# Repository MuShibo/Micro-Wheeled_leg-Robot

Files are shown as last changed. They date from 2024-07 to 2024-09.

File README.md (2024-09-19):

# Micro-Wheeled_leg-Robot
> **The smallest two-wheeled-leg robot!**
>
> Video：[[自制]首款桌面级双轮腿机器人](https://www.bilibili.com/video/BV1io4y1q73L/?spm_id_from=333.999.0.0)
>

| Real Robot | 3D Design |
| --- | --- |
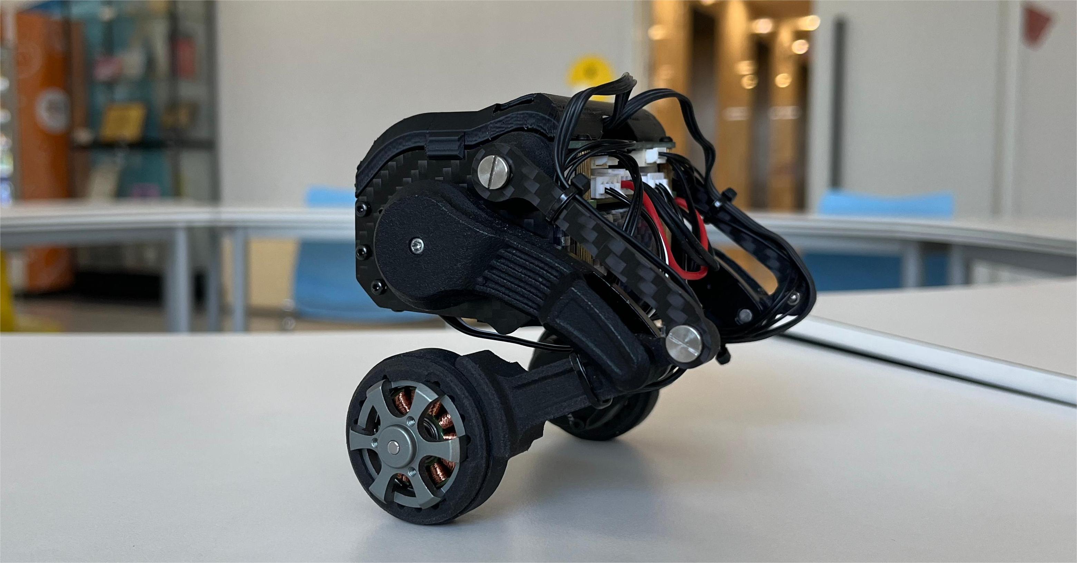
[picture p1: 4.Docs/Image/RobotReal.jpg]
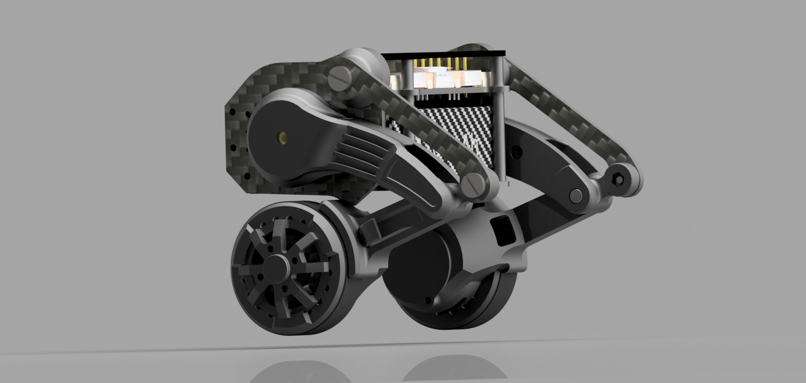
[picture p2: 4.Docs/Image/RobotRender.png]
|  |  |

[中文文档](README_CN.md)

### Mechanical Structure Documentation

* The file "OriginalRobotModel.stp" is the robot model file.
* The "Parts-Manufactured" folder contains parts that need to be processed and produced by yourself, including 3D printing, CNC, and panel cutting.
* The "Parts-Purchased" folder contains parts that need to be purchased.

### PCB Documentation

* There are four PCBs that need to be fabricated; the circuit boards provide both the schematic and PCB source files, and the IDE used is [LCEDA](https://lceda.cn/).
* The main control board is based on the ESP32, with the brushless motor driver chip being the L6234PD013TR. 
* The encoder chip used is the AS5600, communicating with the main control board via the I2C interface.
* The IMU used is the MPU6050 module, which shares the same I2C interface with the right-side encoder.
* The servo debugging board unifies the two serial lines into one signal line, completing the task through time-division multiplexing to send and receive data.
* In addition, you will need three GH1.25 4PIN double-ended cables, with a recommended length of 15cm. These need to be purchased separately.

| Wire Connection | 
| ------------ |
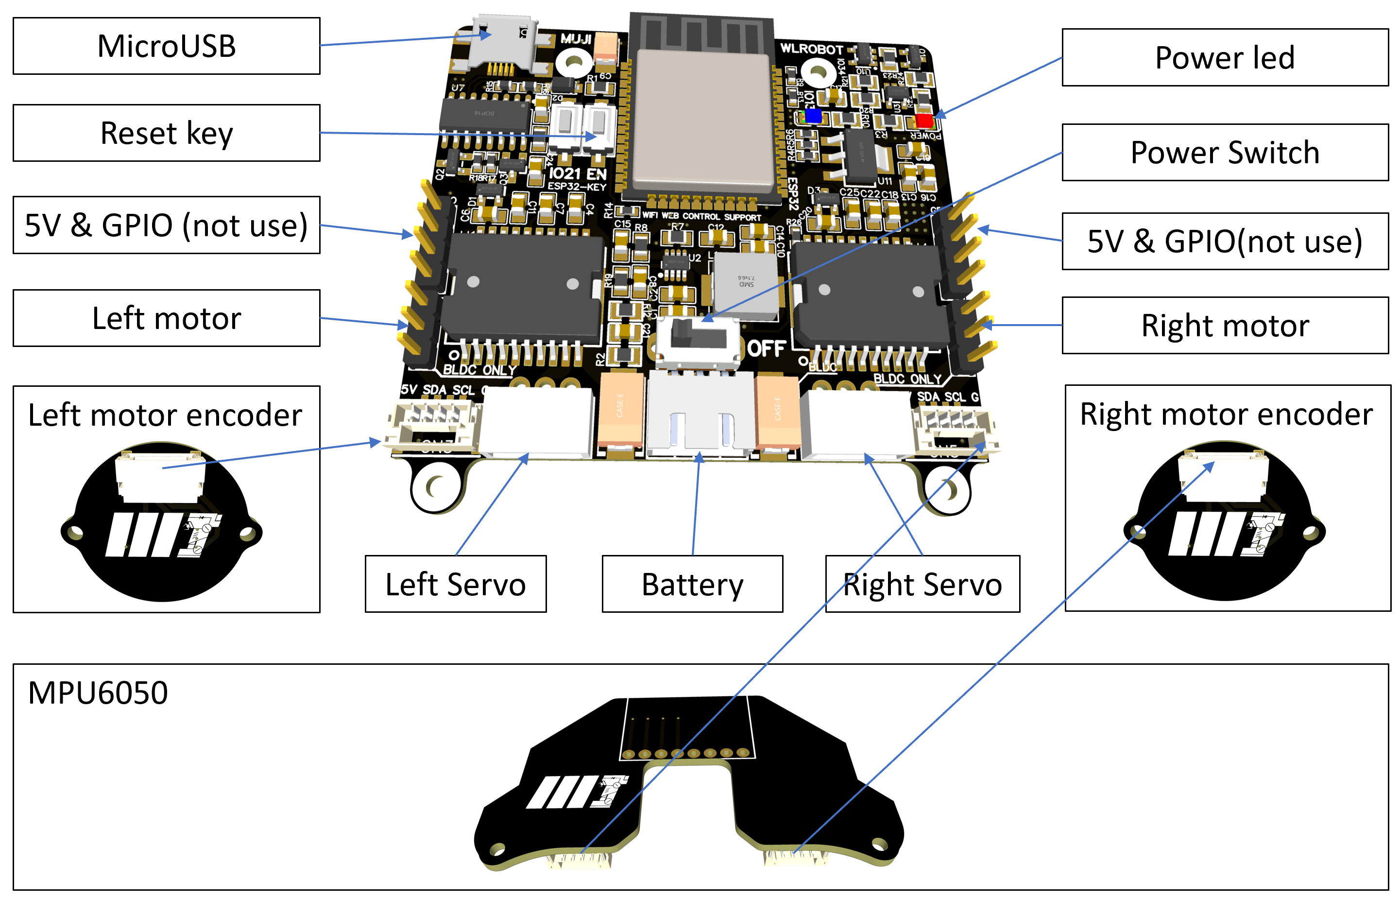
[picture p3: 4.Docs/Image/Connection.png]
|  |

### Source Code Usage

* Based on [Arduino IDE](https://www.arduino.cc/), it is very easy to learn and use.
* The brushless motor drive for the wheels is based on [simpleFOC](https://www.simplefoc.com/#simplefoc_library).
* The left bus servo ID is 1, and the right is 2; the calibration for the legs to fully squat to the mechanical limit position is 2048; configuration is done using [FEETECH Debug Software](https://gitee.com/ftservo/fddebug).
* The [ESP32](https://www.espressif.com/sites/default/files/documentation/esp32_datasheet_en.pdf) itself has WiFi capabilities, with the webpage code stored in flash, transmitting JSON data via the WebSocket communication protocol.
* Please use the WebSocket library located in [3.Software/libraries](3.Software/libraries). The recommended esp32 version is 2.0.3.
* There are two WiFi models, AP mode and STA mode. AP mode uses the device as a wireless hotspot, and STA mode uses the device as a client to connect to an existing wireless network.

### Usage Instructions

* 1. Connect the battery's XH2.54 plug to the rear interface of the main control board and turn on the switch to power the robot.
* 2. After turning on the switch, a red light on the main board will indicate that the power is on.
* 3. Next, the wheels will start FOC motor initialization, with the wheels moving slightly and the legs starting to move.
* 4. If the battery is sufficient, the blue LED on the main control board will light up. If it does not light up, charging is needed.
* 5. After this process is complete, press the EN button on the main control board to restart, and you can then connect to the robot's WiFi network starting with WL. The password is the lowercase WiFi name.
* 6. Open a browser and go to the URL 192.168.1.11. The remote control interface is compatible with Android, iOS, Windows, Linux, macOS, etc., and it is recommended to use Chrome or Firefox.
* 7. Manually stabilize the robot, with the wheels slightly touching the ground. Click the "Robot go!" button on the web page, and the robot will stand up. You can then control the robot's movement using the joystick.

#### Open Source Contributors

* Mu Shibo
* Li Yufeng

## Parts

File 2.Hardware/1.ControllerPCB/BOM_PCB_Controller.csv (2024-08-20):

ID | Name | Designator | Footprint | Quantity | Manufacturer Part | Manufacturer
1 | 4.7K | R26,R4,R5,R6,R9,R13,R14 | R0603 | 7
2 | 0.1uF | C23,C24,C2,C8,C12 | C0805 | 5 |  | LCSC
3 | 1N4007W | D2 | SOD-123_L2.8-W1.8-LS3.7-RD | 1 | 1N4007W | BLUE ROCKET
4 | CH340C | U7 | SOP-16_L10.0-W3.9-P1.27-LS6.0-BL | 1 | CH340C | WCH(南京沁恒)
5 | 0.1uF | C21,C17,C19 | C0805 | 3 | CC0805KRX7R9BB104 | YAGEO
6 | SS-12D02-VG4 | CN7 | SW-TH_SS-12D02-VG4 | 1 | SS-12D02-VG4 | Rectangular Connectors - Contacts
7 | 3K/0.1% | R2 | R0805 | 1 | TC0525B3001T5E | UniOhm
8 | 1k/0.1% | R12 | R0805 | 1 | ARG05BTC1001 | Viking Tech
9 | 5264-3A | H10,H11 | CONN-TH_5264-3AW | 2
10 | SS8050_C541705 | Q2,Q3 | SOT-23-3_L2.9-W1.3-P1.90-LS2.4-BR | 2 | SS8050 | AnBon
11 | 1K | R15,R16 | R0603 | 2 | RMCF0603JT10K0 | Stackpole Elec
12 | 10K | R17,R18 | R0603 | 2 | RMCF0603JT10K0 | Stackpole Elec
13 | HDR-M-2.54_1x4 | J2,J4 | HDR-M-2.54_1X4 | 2
14 | U-C-M5SS-Y-1 | USB2 | MICRO-USB-SMD_U-C-M5SS-Y-1 | 1 | U-C-M5SS-Y-1 | 韩国韩荣
15 | HX25003-3WAP | CN2 | CONN-TH_3P-P2.50_HX25003-3WAP | 1 | HX25003-3WAP | HX(红星)
16 | LED-0805_B | LED2 | LED0805_BLUE | 1 | D-B080508B1-KS2 | 方舟 ARKLED
17 | 1K | R10,R3 | R0805 | 2 | 0805W8F1001T5E | UniOhm
18 | LED-0805_R | LED1 | LED0805_RED | 1 | 17-21SURC/S530-A3/TR8 | EVERLIGHT(台湾亿光)
19 | 10uF | C16,C13 | C0805 | 2 | CL21A106KOQNNNE | SAMSUNG
20 | 22uF | C1,C10,C14 | C0805 | 3
21 | 33pF | C15 | C0805 | 1
22 | 4.7uH | L1 | IND-SMD_L7.3-W6.6 | 1 | MCS0630-4R7MPY1 | PSA(信昌电陶)
23 | SS8550-C148468 | Q1 | SOT-23-3_L2.9-W1.3-P1.90-LS2.4-BR | 1 | SS8550 | Yenji
24 | 100k | R7 | R0805 | 1
25 | 40.2k | R8 | R0805 | 1
26 | 5.49k | R19 | R0805 | 1
27 | 10k | R20,R21,R23,R24 | R0805 | 4 | 0805W8F1002T5E | UniOhm
28 | 10k | R22 | R0805 | 1 | 0805W8F2002T5E | UniOhm
29 | MP2225GJ-Z | U2 | TSOT-23-8_L2.9-W1.6-P0.65-LS2.8-BR | 1 | MP2225GJ-Z | MPS
30 | SN74LVC1G125DBVR | U3 | SOT-23-5_L3.0-W1.7-P0.95-LS2.8-BR | 1 | SN74LVC1G125DBVR | TI
31 | SN74LVC1G126DBVR | U10 | SOT-23-5_L3.0-W1.7-P0.95-LS2.8-BR | 1 | SN74LVC1G126DBVR | TI
32 | 100uF | C9 | CAP-SMD_L3.5-W2.8-R-RD | 1 | CA45-B-6.3V-100uF-M | Shenzhen Zhenhua XinYun Elec
33 | AMS1117-3.3 | U11 | SOT-223_L6.7-W3.5-P2.30-BR | 1 | AMS1117-3.3 | Youtai Semiconductor Co., Ltd.
34 | 100uF | C3,C5 | CAP-SMD_L7.3-W4.3-R-RD | 2 | TAJD107M020RNJ | AVX
35 | A1257WV-S-4P | CN3,CN5 | CONN-SMD_A1257WV-S-4P | 2 | A1257WV-S-4P | Changjiang Connectors
36 | HDR-M-2.54_1x3 | J1,J3 | HDR-M-2.54_1X3 | 2
37 | 10K | R1,R11 | R0805 | 2 | RMCF0603JT10K0 | Stackpole Elec
38 | 100nF | C4,C18 | C0805 | 2 | C0805X104K101T | HEC(Holy Stone Enterprise)
39 | 220nF | C6,C20 | C0805 | 2 | CL21B224KBFNNNE | SAMSUNG
40 | 1uF | C7,C22 | C0805 | 2 | CL21B105KBFNNNE | SAMSUNG
41 | 10nF | C11,C25 | C0805 | 2 | CL21A106KAYNNNE | SAMSUNG
42 | LBAT54SLT1G | D1,D3 | SOT-23_L2.9-W1.3-P1.90-LS2.4-BR | 2 | LBAT54SLT1G | LRC
43 | K2-3.6×6.1_SMD | KEY1,KEY2 | KEY-SMD_2P-L6.2-W3.6-LS8.0 | 2 | K2-1107ST-A4SW-06
44 | L6234PD013TR | U1,U4 | POWERSO20_L15.9-W11.0-P1.27-LS14.2-BL-EP | 2 | L6234PD013TR | STMicroelectronics
45 | ESP32-WROOM-32 | U5 | WIFIM-SMD_ESP-32S | 1 | ESP32-WROOM-32 | Espressif Systems

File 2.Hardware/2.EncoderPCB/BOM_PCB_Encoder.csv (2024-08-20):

ID | Name | Designator | Footprint | Quantity | Manufacturer Part | Manufacturer
1 | GH1.25_4P | J2 | GH1.25_4P_卧贴 | 1 |  | Changjiang Connectors
2 | 100nf | C1 | C0603 | 1
3 | 1uf | C2 | C0603 | 1
4 | 4.7K | R1,R2 | R0603 | 2
5 | AS5600-ASOM | U1 | SOIC-8_L5.0-W4.0-P1.27-LS6.0-BL | 1 | AS5600-ASOM | Ams

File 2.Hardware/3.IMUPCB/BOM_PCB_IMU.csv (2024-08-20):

ID | Name | Designator | Footprint | Quantity | Manufacturer Part | Manufacturer
1 | MPU6050模块 | P2 | MPU6050 | 1
2 | GH1.25_4P | J2,J1 | GH1.25_4P_卧贴 | 2 |  | Changjiang Connectors

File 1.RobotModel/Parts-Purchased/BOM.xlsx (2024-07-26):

Part Name | Recommended Purchase Link | Specifications | Quantity
Joint Actuator | https://item.taobao.com/item.htm?priceTId=2147818c17214662551577531edc58&id=624005504026&ns=1&abbucket=16 | 黑色 STS3032/360° | 2
Wheel Motor | https://item.taobao.com/item.htm?spm=a1z09.2.0.0.6f8c2e8daIyqdB&id=556445606114&_u=k2st8hc2dcef | 零售 | 2
Magnet | https://item.taobao.com/item.htm?id=677927264803&_u=q2st8hc2ca1c&sku_properties=-3:-5 | 直径4mm,厚度1mm | 2
Battery | https://item.taobao.com/item.htm?id=527326501663&_u=k2st8hc287ca&sku_properties=31309:32595472760 | 1100mah | 1
Charger | https://item.taobao.com/item.htm?id=728228890176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 | 平衡锂电充电器 | 1
GB Screws | https://detail.tmall.com/item.htm?id=529656697168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 | M2*4 M2*6 M2.5*5 M3*6 | 20 of each.
GB Nuts | https://detail.tmall.com/item.htm?id=39178267251&rn=b5d916a495226c131bbab29d02221680&abbucket=12 | M2 | 2
Other Screws | https://item.taobao.com/item.htm?spm=a1z09.2.0.0.6f8c2e8daIyqdB&id=538025764032&_u=k2st8hc217d7 | M2.3-0.4*15 | 2
Column_3mm | https://item.taobao.com/item.htm?spm=a1z09.2.0.0.6f8c2e8daIyqdB&id=647328388853&_u=k2st8hc22a77 | M2 x 长3 x 宽3 （贯通牙） | 4
M2x6_BigHead | https://detail.tmall.com/item.htm?id=722946822369&spm=a1z09.2.0.0.6f8c2e8daIyqdB&_u=k2st8hc21ee3 | M2*6 | 4
bearing3-6-2 | https://detail.tmall.com/item.htm?id=611796709407&spm=a1z09.2.0.0.6f8c2e8daIyqdB&_u=k2st8hc2e6c7 | 3*6*2 | 4 | s
bearing4-7-2.5 | https://detail.tmall.com/item.htm?id=611796709407&_u=k2st8hc2e6c7&skuId=4777422306653 | 4*7*2.5 | 4
Pin4-12 | https://detail.tmall.com/item.htm?id=718672136863&spm=a1z09.2.0.0.6f8c2e8daIyqdB&_u=k2st8hc2ae2e | 4X12 | 2
Tire | https://item.taobao.com/item.htm?spm=a1z09.2.0.0.6f8c2e8daIyqdB&id=669383925819&_u=k2st8hc26fde | 直径25宽10mm黑色 | 2
Column_1 | https://detail.tmall.com/item.htm?priceTId=2147804217214673637194390e8199&id=631585716430&xxc=ad_ztc | M2*25+3 | 2
Column_2 | https://detail.tmall.com/item.htm?id=618581380263&spm=a1z09.2.0.0.6f8c2e8daIyqdB&_u=k2st8hc22f44 | M2*8-D3.5MM | 4
Column_3 | https://detail.tmall.com/item.htm?id=19634185206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 | M2*8+3 | 3

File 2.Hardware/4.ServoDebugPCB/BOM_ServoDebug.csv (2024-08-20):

ID | Name | Designator | Footprint | Quantity | Manufacturer Part | Manufacturer
1 | HDR-F-2.54_2x4 | H1 | HDR-F-2.54_2X4 | 1
2 | 0.1uF | C1,C2 | C0805 | 2 | CC0805KRX7R9BB104 | YAGEO
3 | WJ126V-5.0-2P | P3 | CONN-TH_WJ126V-5.0-2P | 1 | WJ126V-5.0-2P | ReliaPro
4 | SS8550 | Q1 | SOT-23_L2.9-W1.3-P0.95-LS2.4-BR | 1 | SS8550 | Slkor(SLKORMICRO Elec.)
5 | 10k | R1,R2,R3,R4,R5 | R0805 | 4 | 0805W8F1002T5E | UniOhm
6 | SN74LVC1G126DBVR | U2 | SOT-23-5_L3.0-W1.7-P0.95-LS2.8-BR | 1 | SN74LVC1G125DBVR | TI
7 | SN74LVC1G125DBVR | U3 | SOT-23-5_L3.0-W1.7-P0.95-LS2.8-BR | 1 | SN74LVC1G125DBVR | TI
8 | 5264-3A | H2 | 5264-3A | 1

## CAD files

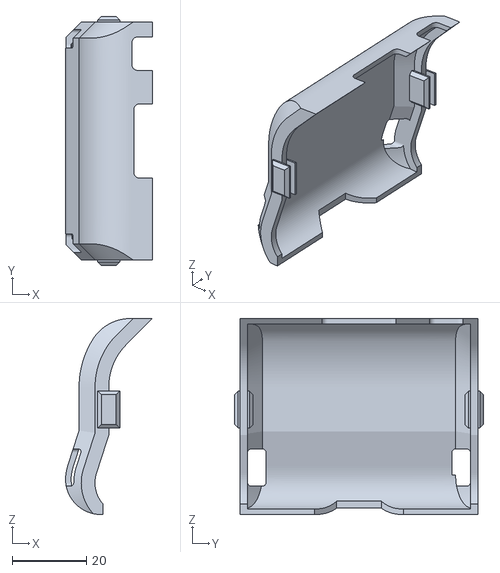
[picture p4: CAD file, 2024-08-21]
1.RobotModel/Parts-Manufactured/1.3DPrint/PCBCover(optional).stl
23.4 x 67.0 x 52.7

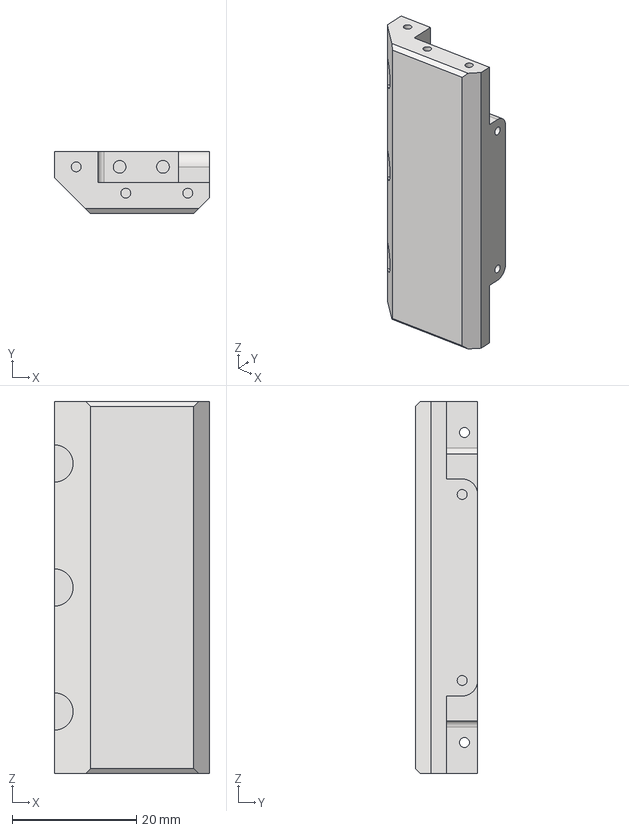
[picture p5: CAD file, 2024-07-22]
1.RobotModel/Parts-Manufactured/2.CNC/BodyBase-Steel.stp
25.0 x 10.1 x 60.0 mm

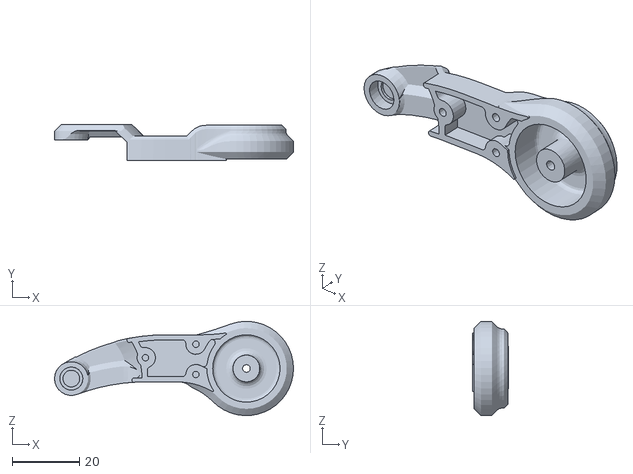
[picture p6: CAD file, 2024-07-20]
1.RobotModel/Parts-Manufactured/1.3DPrint/ThighCover x1.stl
71.0 x 10.8 x 28.0

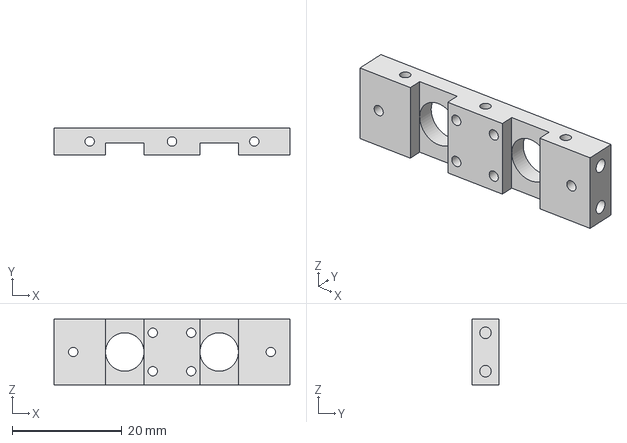
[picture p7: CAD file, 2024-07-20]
1.RobotModel/Parts-Manufactured/2.CNC/MotorBase-Aluminum6061.stp
43.0 x 5.00 x 12.0 mm

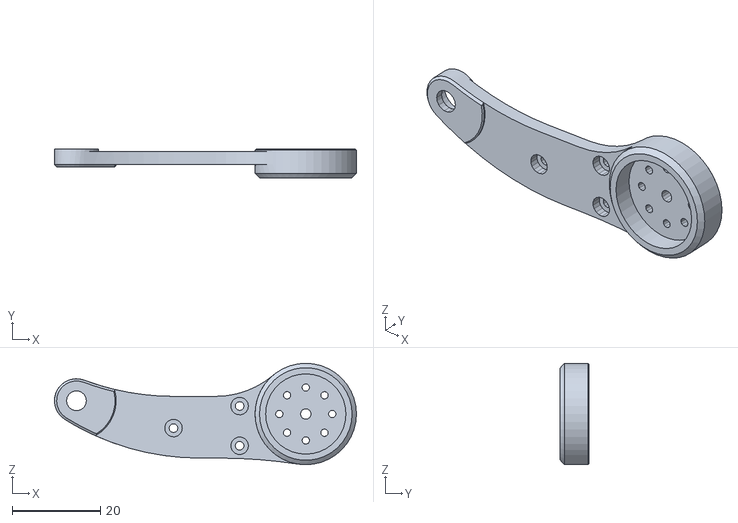
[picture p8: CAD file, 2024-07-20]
1.RobotModel/Parts-Manufactured/1.3DPrint/Thigh_MIR x1.stl
68.5 x 6.50 x 23.0

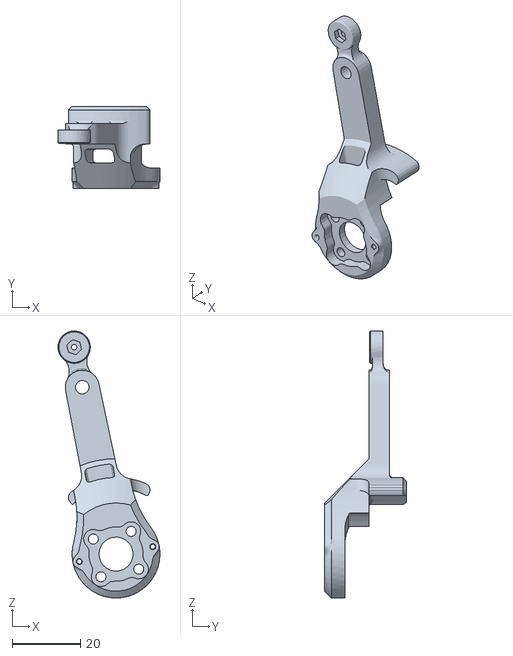
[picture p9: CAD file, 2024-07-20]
1.RobotModel/Parts-Manufactured/1.3DPrint/Calf x1.stl
29.9 x 24.0 x 78.4

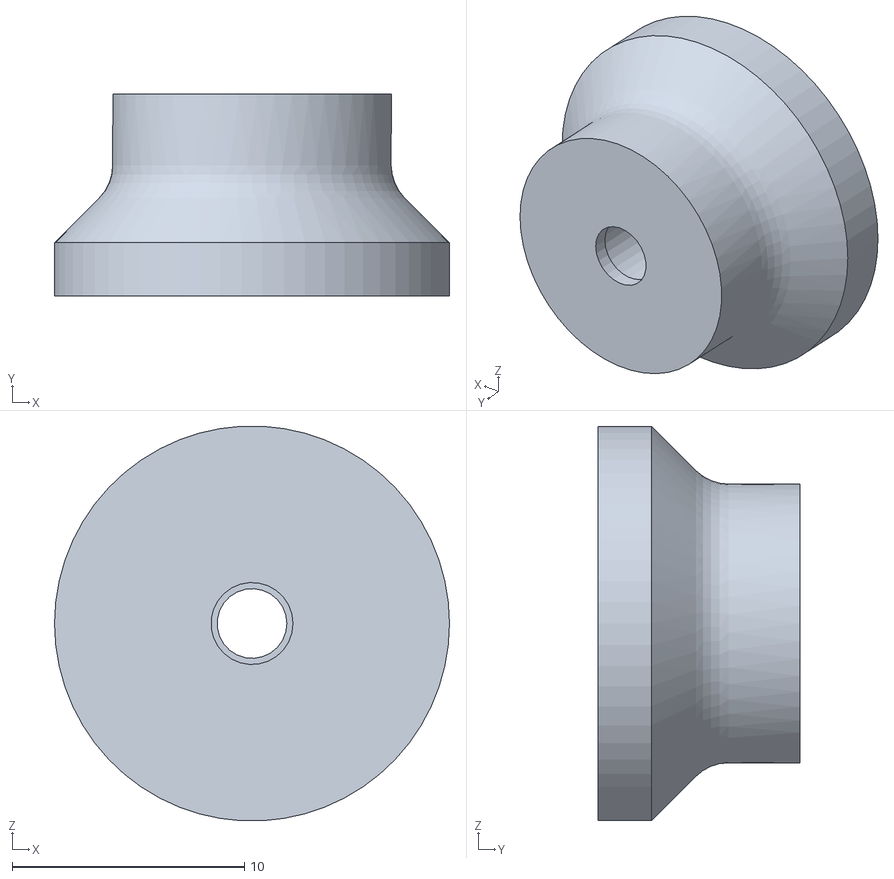
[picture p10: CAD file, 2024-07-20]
1.RobotModel/Parts-Manufactured/1.3DPrint/ColumnCover x2.stl
17.0 x 8.70 x 17.0

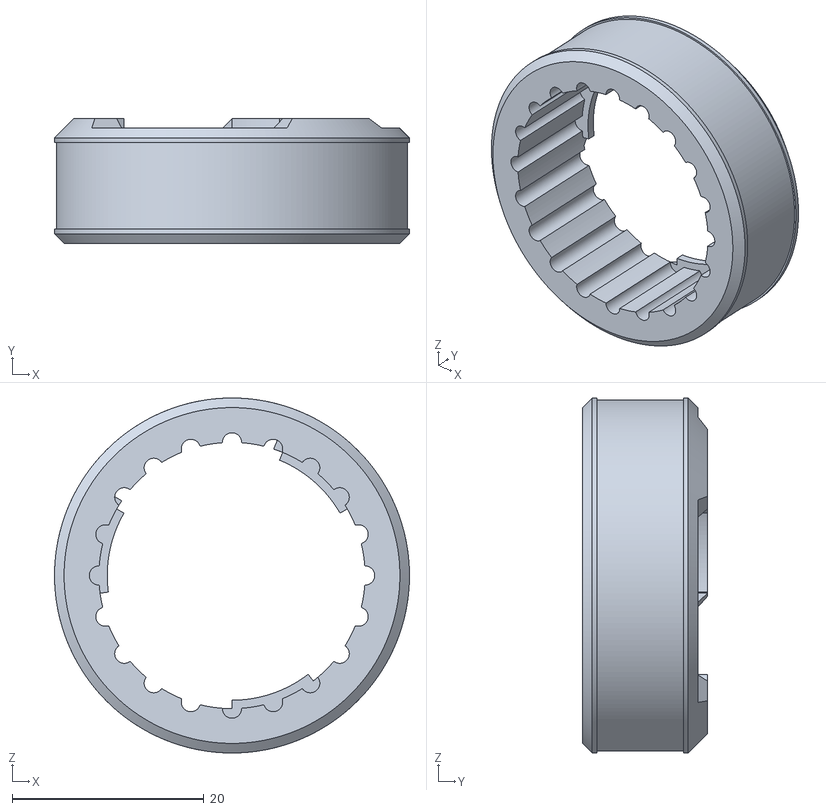
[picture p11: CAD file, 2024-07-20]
1.RobotModel/Parts-Manufactured/1.3DPrint/Hub x2.stl
37.0 x 13.0 x 37.0

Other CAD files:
1.RobotModel/Parts-Manufactured/3.CarbonFiberPanels/Panel.dwg
1.RobotModel/Parts-Manufactured/1.3DPrint/ThighCover_MIR x1.stl
1.RobotModel/Parts-Manufactured/1.3DPrint/Thigh x1.stl
1.RobotModel/Parts-Manufactured/1.3DPrint/Calf_MIR x1.stl

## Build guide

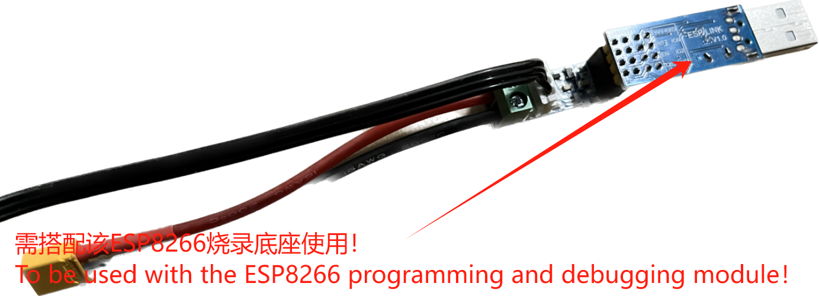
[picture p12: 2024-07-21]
2.Hardware/4.ServoDebugPCB/SpecialInstruction.png

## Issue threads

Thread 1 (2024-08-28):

Could your product  be customized?

autodriving-heart, 2024-08-28:
It was a pleasure to meet your video at 哔哩哔哩. We are interested in customizing a similar product and would like to know if you are open to collaborating with us. My contact information is: AIDriver002 (WeChat). Looking forward to your reply.

Closed 2024-09-20.

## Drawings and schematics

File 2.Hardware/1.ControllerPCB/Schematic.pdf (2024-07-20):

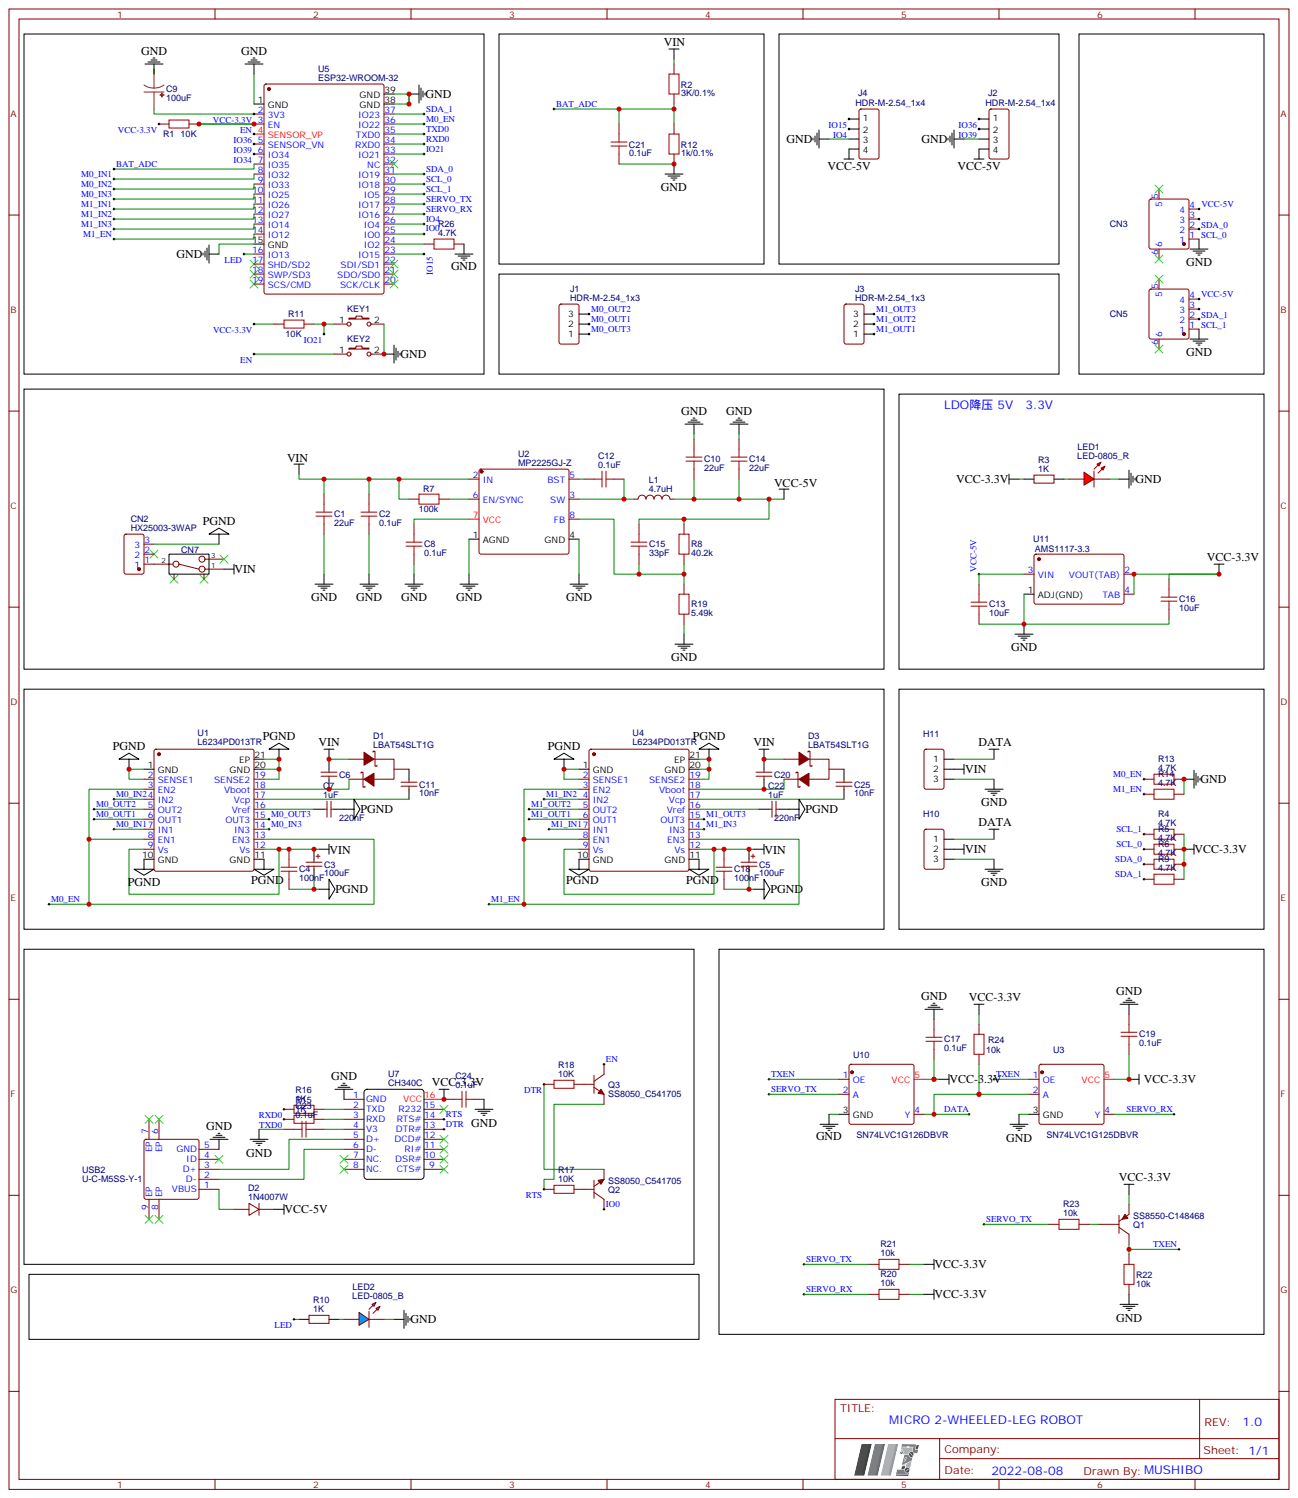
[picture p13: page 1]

MICRO 2-WHEELED-LEG ROBOT

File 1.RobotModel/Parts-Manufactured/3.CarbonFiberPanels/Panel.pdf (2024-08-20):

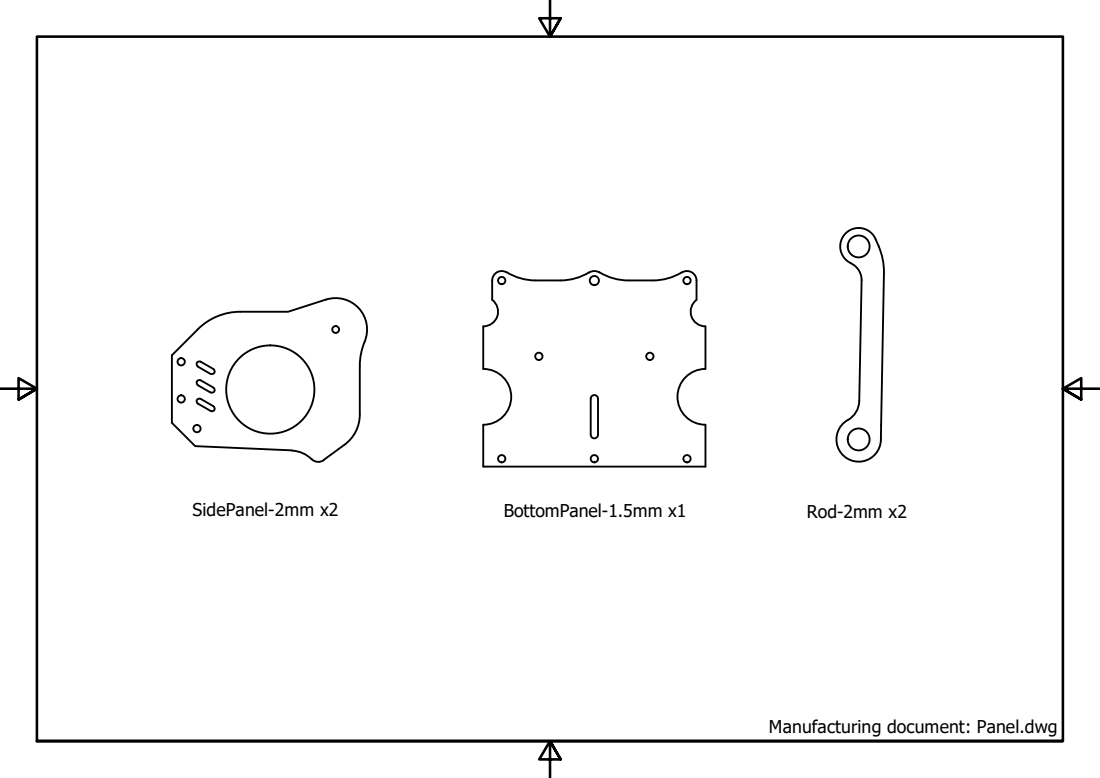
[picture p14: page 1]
SidePanel-2mm x2; BottomPanel-1.5mm x1; Rod-2mm x2

Manufacturing document: Panel.dwg

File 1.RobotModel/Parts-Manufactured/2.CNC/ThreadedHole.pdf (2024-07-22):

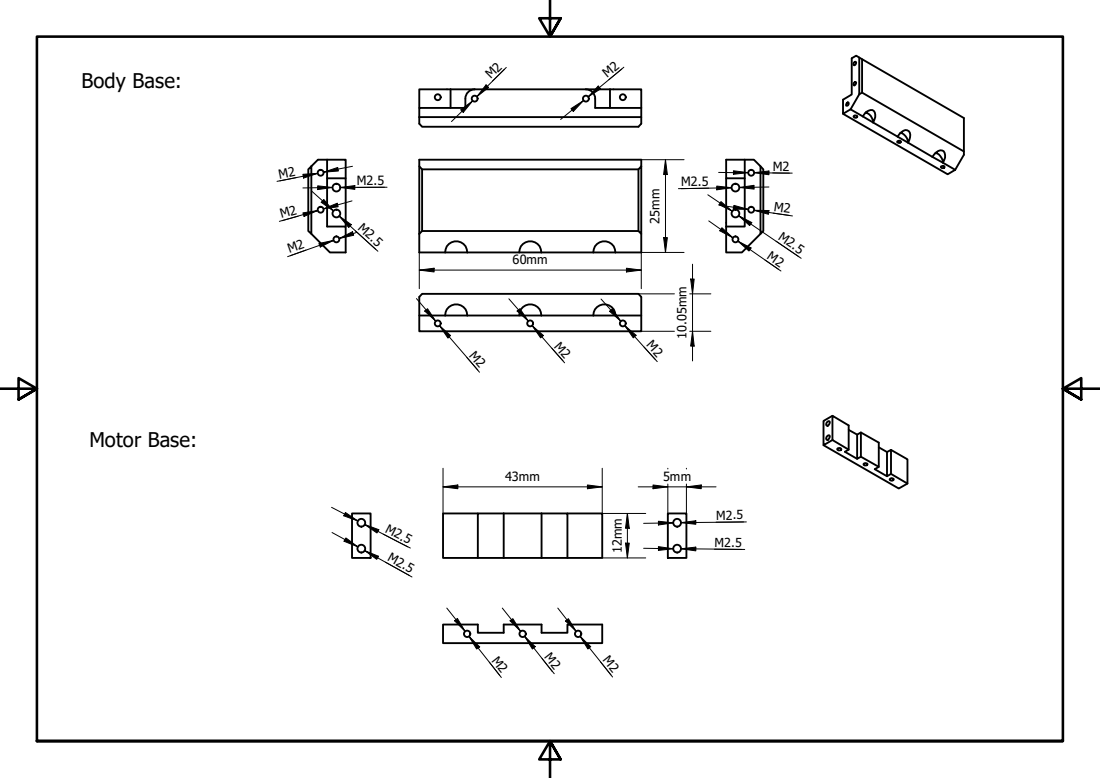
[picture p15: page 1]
Body Base:; Motor Base:

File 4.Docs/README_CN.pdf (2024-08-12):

# Micro-Wheeled_leg-Robot

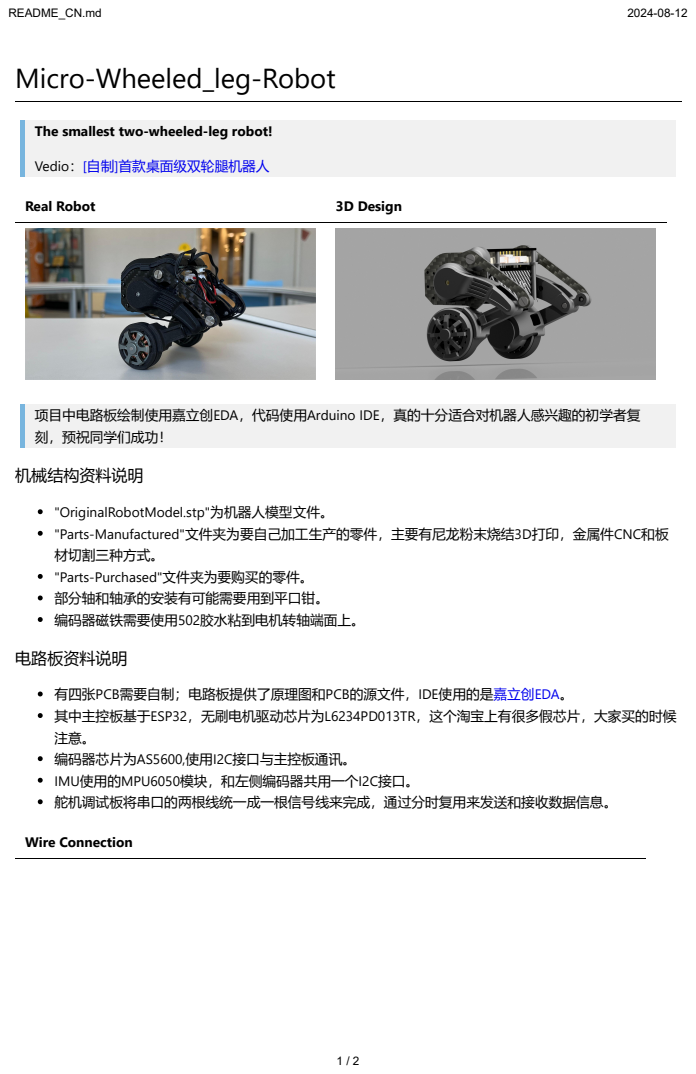
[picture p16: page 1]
README_CN.md; Real Robot; 3D Design; 有四张PCB需要自制；电路板提供了原理图和PCB的源文件，IDE使用的是嘉立创EDA。 其中主控板基于ESP32，无刷电机驱动芯片为L6234PD013TR，这个淘宝上有很多假芯片，大家买的时候 注意。 编码器芯片为AS5600,使用I2C接口与主控板通讯。 IMU使用的MPU6050模块，和左侧编码器共用一个I2C接口。 舵机调试板将串口的两根线统一成一根信号线来完成，通过分时复用来发送和接收数据信息。; Wire Connection

The smallest two-wheeled-leg robot!

Vedio：[自制]首款桌面级双轮腿机器人 (https://www.bilibili.com/video/BV1io4y1q73L/?spm_id_from=333.999.0.0)

项目中电路板绘制使用嘉立创EDA，代码使用Arduino IDE，真的十分适合对机器人感兴趣的初学者复
刻，预祝同学们成功！
机械结构资料说明

"OriginalRobotModel.stp"为机器人模型文件。
"Parts-Manufactured"文件夹为要自己加工生产的零件，主要有尼龙粉末烧结3D打印，金属件CNC和板
材切割三种方式。
"Parts-Purchased"文件夹为要购买的零件。
部分轴和轴承的安装有可能需要用到平口钳。
编码器磁铁需要使用502胶水粘到电机转轴端面上。
电路板资料说明

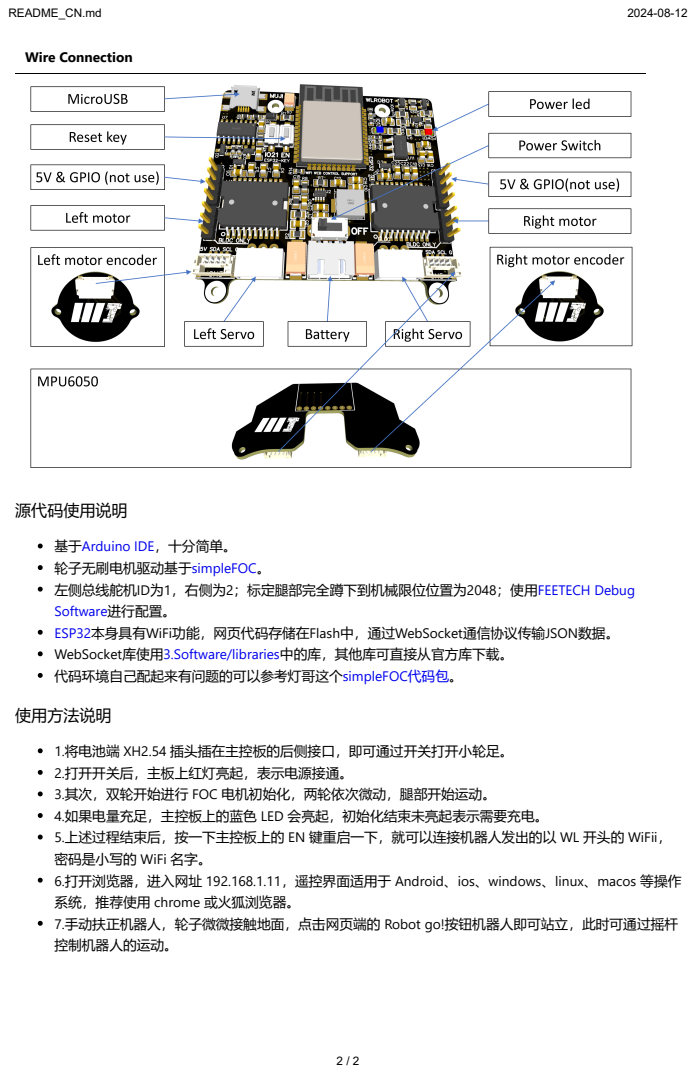
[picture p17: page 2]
README_CN.md; Wire Connection; 源代码使用说明; 使用方法说明

基于Arduino IDE，十分简单。 (https://www.arduino.cc/)
轮子无刷电机驱动基于simpleFOC。 (https://www.simplefoc.com/#simplefoc_library)
左侧总线舵机ID为1，右侧为2；标定腿部完全蹲下到机械限位位置为2048；使用FEETECH Debug
Software进行配置。 (https://gitee.com/ftservo/fddebug)
ESP32本身具有WiFi功能，网页代码存储在Flash中，通过WebSocket通信协议传输JSON数据。 (https://www.espressif.com/sites/default/files/documentation/esp32_datasheet_en.pdf)
WebSocket库使用3.Software/libraries中的库，其他库可直接从官方库下载。
代码环境自己配起来有问题的可以参考灯哥这个simpleFOC代码包。 (https://gitee.com/ream_d/Deng-s-foc-controller/tree/master/Arduino%20IDE%20for%20Deng%20FOC)

1.将电池端 XH2.54 插头插在主控板的后侧接口，即可通过开关打开小轮足。
2.打开开关后，主板上红灯亮起，表示电源接通。
3.其次，双轮开始进行 FOC 电机初始化，两轮依次微动，腿部开始运动。
4.如果电量充足，主控板上的蓝色 LED 会亮起，初始化结束未亮起表示需要充电。
5.上述过程结束后，按一下主控板上的 EN 键重启一下，就可以连接机器人发出的以 WL 开头的 WiFii，
密码是小写的 WiFi 名字。
6.打开浏览器，进入网址 192.168.1.11，遥控界面适用于 Android、ios、windows、linux、macos 等操作
系统，推荐使用 chrome 或火狐浏览器。
7.手动扶正机器人，轮子微微接触地面，点击网页端的 Robot go!按钮机器人即可站立，此时可通过摇杆
控制机器人的运动。

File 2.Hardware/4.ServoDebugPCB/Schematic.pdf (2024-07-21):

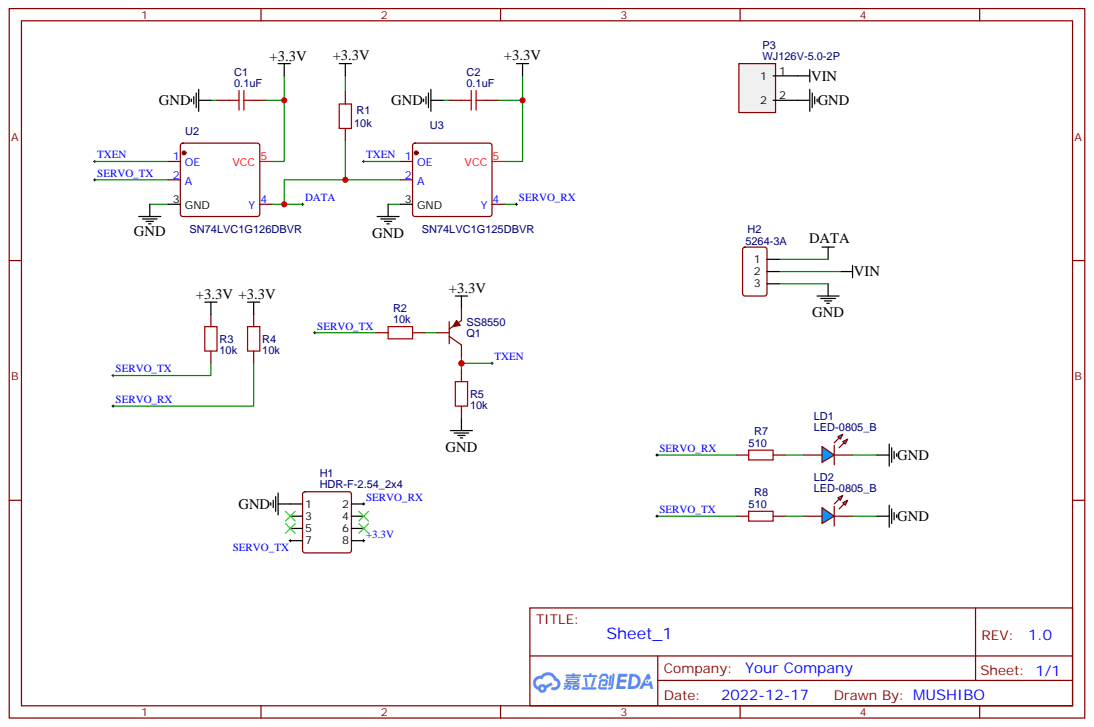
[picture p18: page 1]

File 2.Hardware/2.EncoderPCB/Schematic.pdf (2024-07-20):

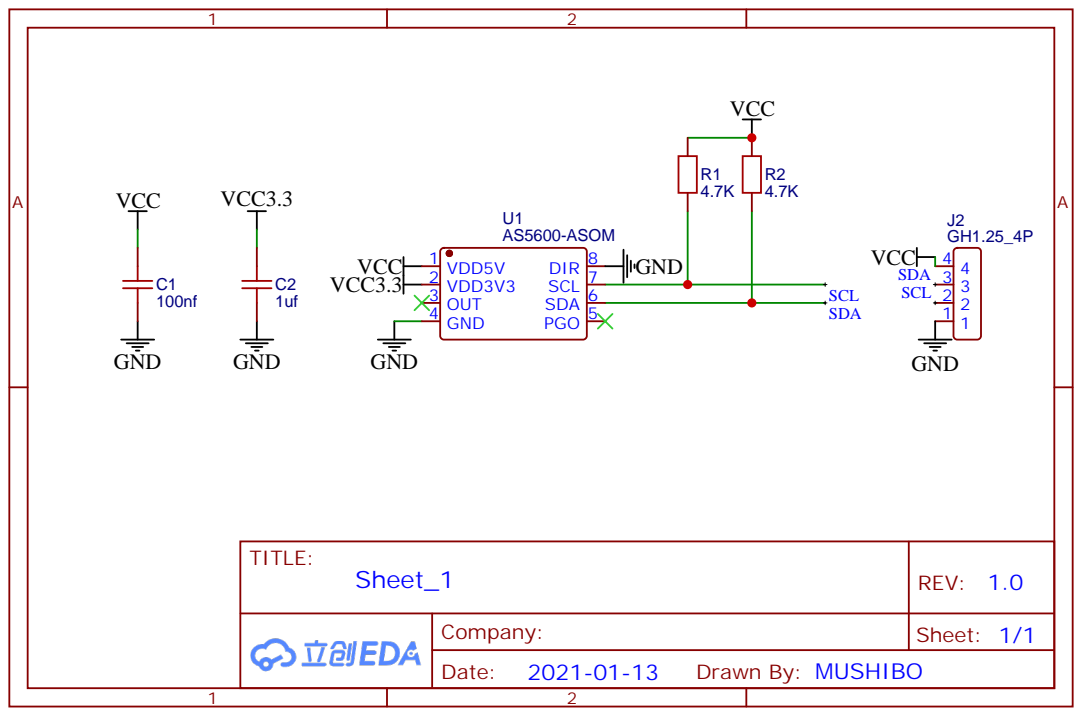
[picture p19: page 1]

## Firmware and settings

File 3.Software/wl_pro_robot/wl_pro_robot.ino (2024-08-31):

// -----------------------------------------------------------------------------
// Copyright (c) 2024 Mu Shibo
// 
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
//机器人控制头文件
#include <MPU6050_tockn.h>
#include "Servo_STS3032.h"
#include <SimpleFOC.h>
#include <Arduino.h>

//wifi控制数据传输头文件
#include <WebSocketsServer.h>
#include <ArduinoJson.h>
#include <WebServer.h>
#include <WiFi.h>
#include <FS.h>
#include "basic_web.h"
#include "robot.h"
#include "wifi.h"
#include "esp_adc_cal.h"

/************实例定义*************/

//电机实例
BLDCMotor motor1 = BLDCMotor(7);
BLDCMotor motor2 = BLDCMotor(7);
BLDCDriver3PWM driver1 = BLDCDriver3PWM(32,33,25,22);
BLDCDriver3PWM driver2  = BLDCDriver3PWM(26,27,14,12);

//编码器实例
TwoWire I2Cone = TwoWire(0);
TwoWire I2Ctwo = TwoWire(1);
MagneticSensorI2C sensor1 = MagneticSensorI2C(AS5600_I2C);
MagneticSensorI2C sensor2 = MagneticSensorI2C(AS5600_I2C);

//PID控制器实例
PIDController pid_angle     {.P = 1,    .I = 0,   .D = 0, .ramp = 100000, .limit = 8};
PIDController pid_gyro      {.P = 0.06, .I = 0,   .D = 0, .ramp = 100000, .limit = 8};
PIDController pid_distance  {.P = 0.5,  .I = 0,   .D = 0, .ramp = 100000, .limit = 8};
PIDController pid_speed     {.P = 0.7,  .I = 0,   .D = 0, .ramp = 100000, .limit = 8};
PIDController pid_yaw_angle {.P = 1.0,  .I = 0,   .D = 0, .ramp = 100000, .limit = 8};
PIDController pid_yaw_gyro  {.P = 0.04, .I = 0,   .D = 0, .ramp = 100000, .limit = 8};
PIDController pid_lqr_u     {.P = 1,    .I = 15,  .D = 0, .ramp = 100000, .limit = 8};
PIDController pid_zeropoint {.P = 0.002,.I = 0,   .D = 0, .ramp = 100000, .limit = 4};
PIDController pid_roll_angle{.P = 8,    .I = 0,   .D = 0, .ramp = 100000, .limit = 450};

//低通滤波器实例
LowPassFilter lpf_joyy{.Tf = 0.2};
LowPassFilter lpf_zeropoint{.Tf = 0.1};
LowPassFilter lpf_roll{.Tf = 0.3};

// commander通信实例
Commander command = Commander(Serial);

void StabAngle(char* cmd)     { command.pid(&pid_angle, cmd);     }
void StabGyro(char* cmd)      { command.pid(&pid_gyro, cmd);      }
void StabDistance(char* cmd)  { command.pid(&pid_distance, cmd);  }
void StabSpeed(char* cmd)     { command.pid(&pid_speed, cmd);     }
void StabYawAngle(char* cmd)  { command.pid(&pid_yaw_angle, cmd); }
void StabYawGyro(char* cmd)   { command.pid(&pid_yaw_gyro, cmd);  }
void lpfJoyy(char* cmd)       { command.lpf(&lpf_joyy, cmd);      }
void StabLqrU(char* cmd)      { command.pid(&pid_lqr_u, cmd);     }
void StabZeropoint(char* cmd) { command.pid(&pid_zeropoint, cmd); }
void lpfZeropoint(char* cmd)  { command.lpf(&lpf_zeropoint, cmd); }
void StabRollAngle(char* cmd) { command.pid(&pid_roll_angle, cmd);}
void lpfRoll(char* cmd)       { command.lpf(&lpf_roll, cmd);      }

//void Stabtest_zeropoint(char* cmd) { command.pid(&test_zeropoint, cmd); }

//WebServer实例
WebServer webserver; // server服务器
WebSocketsServer websocket = WebSocketsServer(81); // 定义一个webSocket服务器来处理客户发送的消息
RobotProtocol rp(20);
int joystick_value[2];

//STS舵机实例
SMS_STS sms_sts;

//MPU6050实例
MPU6050 mpu6050(I2Ctwo);

/************参数定义*************/
#define pi 3.1415927

//LQR自平衡控制器参数
float LQR_angle = 0;
float LQR_gyro  = 0;
float LQR_speed = 0;
float LQR_distance = 0;
float angle_control   = 0;
float gyro_control    = 0;
float speed_control   = 0;
float distance_control = 0;
float LQR_u = 0;
float angle_zeropoint = -2.25;
float distance_zeropoint = -256.0;       //轮部位移零点偏置（-256为一个不可能的位移值，将其作为未刷新的标志）

//YAW轴控制数据
float YAW_gyro = 0;
float YAW_angle = 0;
float YAW_angle_last = 0;
float YAW_angle_total = 0;
float YAW_angle_zero_point = -10;
float YAW_output = 0;

//腿部舵机控制数据
byte ID[2];
s16 Position[2];
u16 Speed[2];
byte ACC[2];

//逻辑处理标志位
float robot_speed = 0;          //记录当前轮部转速
float robot_speed_last = 0;     //记录上一时刻的轮部转速
int wrobot_move_stop_flag = 0;  //记录摇杆停止的标识
int jump_flag = 0;              //跳跃时段标识
float leg_position_add = 0;     //roll轴平衡控制量
int uncontrolable = 0;          //机身倾角过大导致失控

//电压检测
uint16_t bat_check_num = 0;
int BAT_PIN = 35;    // select the input pin for the ADC
static esp_adc_cal_characteristics_t adc_chars;
static const adc1_channel_t channel = ADC1_CHANNEL_7;     
static const adc_bits_width_t width = ADC_WIDTH_BIT_12;
static const adc_atten_t atten = ADC_ATTEN_DB_11;
static const adc_unit_t unit = ADC_UNIT_1;

//电量显示LED
#define LED_BAT 13

void setup() {
  Serial.begin(115200);//通讯串口
  Serial2.begin(1000000);//腿部sts舵机

  //Wifi初始化
  WiFi_SetAP();
  // set_sta_wifi();      // ESP-01S STA模式接入WiFi网络
  webserver.begin();
  webserver.on("/", HTTP_GET, basicWebCallback);
  websocket.begin();
  websocket.onEvent(webSocketEventCallback);

  //舵机初始化
  //舵机有效行程450
  //左侧舵机[2048+12+50,2048+12+450]
  //左侧舵机[2048-12-50,2048-12-450]
  sms_sts.pSerial = &Serial2;
  ID[0] = 1;
  ID[1] = 2;
  ACC[0] = 30;
  ACC[1] = 30;
  Speed[0] = 300;
  Speed[1] = 300;  
  Position[0] = 2148;
  Position[1] = 1948;
  //舵机(ID1/ID2)以最高速度V=2400步/秒，加速度A=50(50*100步/秒^2)，运行至各自的Position位置
  sms_sts.SyncWritePosEx(ID, 2, Position, Speed, ACC);

  //电压检测
  adc_calibration_init();
  adc1_config_width(width);
  adc1_config_channel_atten(channel, atten);
  esp_adc_cal_characterize(unit, atten, width, 0, &adc_chars);

  //电量显示LED
  pinMode(LED_BAT,OUTPUT);
  
  // 编码器设置
  I2Cone.begin(19,18, 400000UL); 
  I2Ctwo.begin(23,5, 400000UL); 
  sensor1.init(&I2Cone);
  sensor2.init(&I2Ctwo);

  //mpu6050设置
  mpu6050.begin();
  mpu6050.calcGyroOffsets(true);
  
  //连接motor对象与编码器对象
  motor1.linkSensor(&sensor1);
  motor2.linkSensor(&sensor2);

  //速度环PID参数
  motor1.PID_velocity.P = 0.05;
  motor1.PID_velocity.I = 1;
  motor1.PID_velocity.D = 0;

  motor2.PID_velocity.P = 0.05;
  motor2.PID_velocity.I = 1;
  motor2.PID_velocity.D = 0;

  // 驱动器设置
  motor1.voltage_sensor_align = 6;
  motor2.voltage_sensor_align = 6;
  driver1.voltage_power_supply = 8;
  driver2.voltage_power_supply = 8;
  driver1.init();
  driver2.init();

  //连接motor对象与驱动器对象
  motor1.linkDriver(&driver1);
  motor2.linkDriver(&driver2);

  motor1.torque_controller = TorqueControlType::voltage;
  motor2.torque_controller = TorqueControlType::voltage;   
  motor1.controller = MotionControlType::torque;
  motor2.controller = MotionControlType::torque;
  
  // monitor相关设置
  motor1.useMonitoring(Serial);
  motor2.useMonitoring(Serial);
  //电机初始化
  motor1.init();
  motor1.initFOC(); 
  motor2.init();
  motor2.initFOC();

  // 映射电机到commander
    command.add('A', StabAngle, "pid angle");
    command.add('B', StabGyro, "pid gyro");
    command.add('C', StabDistance, "pid distance");
    command.add('D', StabSpeed, "pid speed");
    command.add('E', StabYawAngle, "pid yaw angle");
    command.add('F', StabYawGyro, "pid yaw gyro");
    command.add('G', lpfJoyy, "lpf joyy");
    command.add('H', StabLqrU, "pid lqr u");
    command.add('I', StabZeropoint, "pid zeropoint");
    command.add('J', lpfZeropoint, "lpf zeropoint");
    command.add('K', StabRollAngle, "pid roll angle");
    command.add('L', lpfRoll, "lpf roll");

    //command.add('M', Stabtest_zeropoint, "test_zeropoint");



  delay(500);
}

void loop() {
  bat_check();        //电压检测
  web_loop();         //Web数据更新
  mpu6050.update();   //IMU数据更新
  lqr_balance_loop(); //lqr自平衡控制
  yaw_loop();         //yaw轴转向控制
  leg_loop();         //腿部动作控制
  
  //将自平衡计算输出转矩赋给电机
  motor1.target = (-0.5)*(LQR_u + YAW_output);
  motor2.target = (-0.5)*(LQR_u - YAW_output);

  //倒地失控后关闭输出
  if( abs(LQR_angle) > 25.0f  )
  {
    uncontrolable = 1;
  }
  if( uncontrolable != 0 )//扶起后延时恢复
  {
    if( abs(LQR_angle) < 10.0f  )
    {
      uncontrolable++;
    }
    if( uncontrolable > 200 )//200次程序循环的延时时间
    {
      uncontrolable = 0;
    }
  }
  
  //关停输出（遥控停止或角度过大失控）
  if(wrobot.go==0 || uncontrolable!=0)
  {
    motor1.target = 0;
    motor2.target = 0;
    leg_position_add = 0;
  }
  
  //记录上一次的遥控数据数据
  wrobot.dir_last  = wrobot.dir;
  wrobot.joyx_last = wrobot.joyx;
  wrobot.joyy_last = wrobot.joyy;
  
  //迭代计算FOC相电压
  motor1.loopFOC();
  motor2.loopFOC();
  
  //设置轮部电机输出
  motor1.move();
  motor2.move();
  
  command.run();
  }

//lqr自平衡控制
void lqr_balance_loop(){
  //LQR平衡算式，实际使用中为便于调参，讲算式分解为4个P控制，采用PIDController方法在commander中实时调试
  //QR_u = LQR_k1*(LQR_angle - angle_zeropoint) + LQR_k2*LQR_gyro + LQR_k3*(LQR_distance - distance_zeropoint) + LQR_k4*LQR_speed;

  //给负值是因为按照当前的电机接线，正转矩会向后转
  LQR_distance  = (-0.5) *(motor1.shaft_angle + motor2.shaft_angle);
  LQR_speed     = (-0.5) *(motor1.shaft_velocity + motor2.shaft_velocity);
  LQR_angle = (float)mpu6050.getAngleY();
  LQR_gyro  = (float)mpu6050.getGyroY(); 
  //Serial.println(LQR_distance); 

  //计算自平衡输出
  angle_control     = pid_angle(LQR_angle - angle_zeropoint);
  gyro_control      = pid_gyro(LQR_gyro);

  //运动细节优化处理
  if(wrobot.joyy != 0)//有前后方向运动指令时的处理
  {
    distance_zeropoint = LQR_distance;//位移零点重置
    pid_lqr_u.error_prev = 0;         //输出积分清零
  }

  if( (wrobot.joyx_last!=0 && wrobot.joyx==0) || (wrobot.joyy_last!=0 && wrobot.joyy==0) )//运动指令复零时的原地停车处理
  {
    wrobot_move_stop_flag = 1;
  }
  if( (wrobot_move_stop_flag==1) && (abs(LQR_speed)<0.5) )
  {
    distance_zeropoint = LQR_distance;//位移零点重置
    wrobot_move_stop_flag = 0;
  }

  if( abs(LQR_speed)>15 )//被快速推动时的原地停车处理
  {
    distance_zeropoint = LQR_distance;//位移零点重置
  }

  //计算位移控制输出
  distance_control  = pid_distance(LQR_distance - distance_zeropoint);
  speed_control     = pid_speed(LQR_speed- 0.1*lpf_joyy(wrobot.joyy) );

  //轮部离地检测
  robot_speed_last = robot_speed; //记录连续两次的轮部转速
  robot_speed = LQR_speed;
  if( abs(robot_speed-robot_speed_last) > 10 || abs(robot_speed) > 50 || (jump_flag != 0))  //若轮部角速度、角加速度过大或处于跳跃后的恢复时期，认为出现轮部离地现象，需要特殊处理
  {
    distance_zeropoint = LQR_distance;    //位移零点重置
    LQR_u = angle_control + gyro_control; //轮部离地情况下，对轮部分量不输出；反之，正常状态下完整输出平衡转矩
    pid_lqr_u.error_prev = 0; //输出积分清零
  }
  else
  {
    LQR_u = angle_control + gyro_control + distance_control + speed_control; 
  }
  
  //触发条件：遥控器无信号输入、轮部位移控制正常介入、不处于跳跃后的恢复时期
  if( abs(LQR_u)<5 && wrobot.joyy == 0 && abs(distance_control)<4 && (jump_flag == 0))
  {
    
    LQR_u = pid_lqr_u(LQR_u);//补偿小转矩非线性
    //Serial.println(LQR_u);
    angle_zeropoint -= pid_zeropoint(lpf_zeropoint(distance_control));//重心自适应
  }
  else
  {
    pid_lqr_u.error_prev = 0; //输出积分清零
  }

  //平衡控制参数自适应
  if(wrobot.height < 50)
  {
    pid_speed.P = 0.7;
  }
  else if(wrobot.height < 64)
  {
    pid_speed.P = 0.6;
  }
  else
  {
    pid_speed.P = 0.5;
  }
}

//腿部动作控制
void leg_loop(){
  jump_loop();
  if(jump_flag == 0)//不处于跳跃状态
  {
    //机身高度自适应控制
    ACC[0] = 8;
    ACC[1] = 8;
    Speed[0] = 200;
    Speed[1] = 200;
    float roll_angle  = (float)mpu6050.getAngleX() + 2.0;
    //leg_position_add += pid_roll_angle(roll_angle);
    leg_position_add = pid_roll_angle(lpf_roll(roll_angle));//test
    Position[0] = 2048 + 12 + 8.4*(wrobot.height-32) - leg_position_add;
    Position[1] = 2048 - 12 - 8.4*(wrobot.height-32) - leg_position_add;
    if( Position[0]<2110 )
      Position[0]=2110;
    else if( Position[0]>2510 )
      Position[0]=2510;
    if( Position[1]<1586 )
      Position[1]=1586;
    else if( Position[1]>1986 )
      Position[1]=1986;
    sms_sts.SyncWritePosEx(ID, 2, Position, Speed, ACC);
  }  
}

//跳跃控制
void jump_loop(){
  if( (wrobot.dir_last == 5) && (wrobot.dir == 4) && (jump_flag == 0) )
  {
      ACC[0] = 0;
      ACC[1] = 0;
      Speed[0] = 0;
      Speed[1] = 0;
      Position[0] = 2048 + 12 + 8.4*(80-32);
      Position[1] = 2048 - 12 - 8.4*(80-32);
      sms_sts.SyncWritePosEx(ID, 2, Position, Speed, ACC);

      jump_flag = 1;
  }
  if( jump_flag > 0 )
  {
    jump_flag++;
    if( (jump_flag > 30) && (jump_flag < 35) )
    {
      ACC[0] = 0;
      ACC[1] = 0;
      Speed[0] = 0;
      Speed[1] = 0;
      Position[0] = 2048 + 12 + 8.4*(40-32);
      Position[1] = 2048 - 12 - 8.4*(40-32);
      sms_sts.SyncWritePosEx(ID, 2, Position, Speed, ACC);

      jump_flag = 40;
    }
    if(jump_flag > 200)
    {
      jump_flag = 0;//已准备好再次跳跃
    }
  }
}

//yaw轴转向控制
void yaw_loop(){
  //YAW_output = 0.03*(YAW_Kp*YAW_angle_total + YAW_Kd*YAW_gyro);
  yaw_angle_addup();
  
  YAW_angle_total += wrobot.joyx*0.002;
  float yaw_angle_control = pid_yaw_angle(YAW_angle_total);
  float yaw_gyro_control  = pid_yaw_gyro(YAW_gyro);
  YAW_output = yaw_angle_control + yaw_gyro_control;  
}

//Web数据更新
void web_loop(){
  webserver.handleClient();
  websocket.loop();
  rp.spinOnce();//更新web端回传的控制信息
}

//yaw轴角度累加函数
void yaw_angle_addup() {
  YAW_angle  = (float)mpu6050.getAngleZ();;
  YAW_gyro   = (float)mpu6050.getGyroZ();

  if(YAW_angle_zero_point == (-10))
  {
    YAW_angle_zero_point = YAW_angle;
  }

  float yaw_angle_1,yaw_angle_2,yaw_addup_angle;
  if(YAW_angle > YAW_angle_last)
  {
    yaw_angle_1 = YAW_angle - YAW_angle_last;
    yaw_angle_2 = YAW_angle - YAW_angle_last - 2*PI;
  }
  else
  {
    yaw_angle_1 = YAW_angle - YAW_angle_last;
    yaw_angle_2 = YAW_angle - YAW_angle_last + 2*PI;
  }

  if(abs(yaw_angle_1)>abs(yaw_angle_2))
  {
    yaw_addup_angle=yaw_angle_2;
  }
  else
  {
    yaw_addup_angle=yaw_angle_1;
  }

  YAW_angle_total = YAW_angle_total + yaw_addup_angle;
  YAW_angle_last = YAW_angle;
}

void basicWebCallback(void)
{
  webserver.send(300, "text/html", basic_web);
}

void webSocketEventCallback(uint8_t num, WStype_t type, uint8_t *payload, size_t length)
{
  if(type == WStype_TEXT)
  {
    String payload_str = String((char*) payload);   
    StaticJsonDocument<300> doc;  
    DeserializationError error = deserializeJson(doc, payload_str);

    String mode_str = doc["mode"];
    if(mode_str == "basic")
    {
      rp.parseBasic(doc);
    }
  }
}

//电压检测初始化
void adc_calibration_init()
{
    if (esp_adc_cal_check_efuse(ESP_ADC_CAL_VAL_EFUSE_TP) == ESP_OK) {
        printf("eFuse Two Point: Supported\n");
    } else {
        printf("eFuse Two Point: NOT supported\n");
    }
    //Check Vref is burned into eFuse
    if (esp_adc_cal_check_efuse(ESP_ADC_CAL_VAL_EFUSE_VREF) == ESP_OK) {
        printf("eFuse Vref: Supported\n");
    } else {
        printf("eFuse Vref: NOT supported\n");
    }
}

//电压检测
void bat_check()
{
  if(bat_check_num > 1000)
  {
    //电压读取
    uint32_t sum = 0;
    sum= analogRead(BAT_PIN);
    uint32_t voltage = esp_adc_cal_raw_to_voltage(sum, &adc_chars);
    double battery=(voltage*3.97)/1000.0;

    Serial.println(battery);
    //电量显示
    if(battery>7.8)
      digitalWrite(LED_BAT,HIGH);
    else
      digitalWrite(LED_BAT,LOW);

    bat_check_num = 0;
  }
  else
    bat_check_num++;
}

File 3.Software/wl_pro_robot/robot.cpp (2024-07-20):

// -----------------------------------------------------------------------------
// Copyright (c) 2024 Mu Shibo
// 
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
#include "robot.h"

Wrobot wrobot;
RobotProtocol::RobotProtocol(uint8_t len)
{
    _len = len;
    _now_buf = new uint8_t[_len];
    _old_buf = new uint8_t[_len];

    for(int i=0;i<_len;i++) {
        _now_buf[i] = 0;
    }

    _now_buf[0] = 0xAA;
    _now_buf[1] = 0x55;
}

RobotProtocol::~RobotProtocol()
{
    delete [] _now_buf;
    delete [] _old_buf;
}

void RobotProtocol::spinOnce(void)
{
    int flag = checkBufRefresh();
    if(flag) 
    {
        //UART_WriteBuf(); //这个会将web端的控制信息转成串口协议发出

        //Serial.println(wrobot.dir);//测试数据获取
        //Serial.println("date have send\n");
        //Serial.printf("height:%d\n", wrobot.height);
        //Serial.printf("roll:%d\n", wrobot.pitch);
        //Serial.printf("linear:%d\n", wrobot.linear);
//        Serial.printf("\n");
//        Serial.printf("joy_X:%d\n", wrobot.joyx);
//        Serial.printf("joy_Y:%d\n", wrobot.joyy);
    }
}









/**************如下同时用于串口输出控制协议***************/

void RobotProtocol::UART_WriteBuf(void)
{
    for(int i=0; i<_len; i++) {
        Serial.write(_now_buf[i]);
    }
}

int RobotProtocol::checkBufRefresh(void)
{
    int ret = 0;
    for(int i=0; i<_len; i++)
    {
        if(_now_buf[i] != _old_buf[i]) {
            ret = 1;
            break;
        }else {
            ret = 0;
        }
    }

    for(int i=0; i<_len; i++) {
        _old_buf[i]= _now_buf[i];
    }
    return ret;
}

void RobotProtocol::parseBasic(StaticJsonDocument<300> &doc)
{
 
    _now_buf[2] = BASIC;

    String dir = doc["dir"];
    if(dir == "stop") {
        _now_buf[3] = STOP;
        wrobot.dir = STOP;  
    } else {
        if(dir == "jump") {      	
            _now_buf[3] = JUMP;
            wrobot.dir = JUMP;
        }else if(dir == "forward") { 
            _now_buf[3] = FORWARD; 
            wrobot.dir = FORWARD;
        }else if(dir == "back") { 	
            _now_buf[3] = BACK; 
            wrobot.dir = BACK;
        }else if(dir == "left") { 	
            _now_buf[3] = LEFT;
            wrobot.dir = LEFT;
        }else if(dir == "right") { 
            _now_buf[3] = RIGHT;
            wrobot.dir = RIGHT;
        }else{
            _now_buf[3] = STOP;
            wrobot.dir = STOP;
        }
    }

    int height = doc["height"];
    _now_buf[4] = height;
    wrobot.height = height;

    int roll = doc["roll"];
    wrobot.roll = roll;
    if(roll >= 0) {
        _now_buf[5] = 0;
    }else {
        _now_buf[5] = 1;
    }
    _now_buf[6] = abs(roll);    
    
    int linear = doc["linear"];
    wrobot.linear = linear;
    if(linear >= 0) {
        _now_buf[7] = 0;
    }else {
        _now_buf[7] = 1;
    }
    _now_buf[8] = abs(linear); 
    
    int angular = doc["angular"];
    wrobot.angular = angular;
    if(angular >= 0) {
        _now_buf[9] = 0;
    }else {
        _now_buf[9] = 1;
    }
    _now_buf[10] = abs(angular); 
   

    int stable = doc["stable"];
    wrobot.go = stable;
    if(stable) {
        _now_buf[11] = 1;
    }else {
        _now_buf[11] = 0;
    }
    
    int joy_x = doc["joy_x"];
    wrobot.joyx = joy_x;
    if(joy_x >= 0) {
        _now_buf[12] = 0;
    }else {
        _now_buf[12] = 1;
    }
    _now_buf[13] = abs(joy_x); 


    int joy_y = doc["joy_y"];
    wrobot.joyy = joy_y;
    if(joy_y >= 0) {
        _now_buf[14] = 0;
    }else {
        _now_buf[14] = 1;
    }
    _now_buf[15] = abs(joy_y); 
}

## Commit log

2024-07-20 Open source demo.
    [BOM.xlsx, BOM_PCB_Controller.csv, BOM_PCB_Encoder.csv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]
2024-07-21 Add servo debug PCB.
    [BOM_ServoDebug.csv, PCB_ServoDebug.json, SCH_ServoDebug.json]
2024-07-22 Update cnc part.
    [BodyBase-Steel.stp]
2024-07-26 Update purchase link of bearing.
    [BOM.xlsx]
2024-07-26 Update purchase link.
    [BOM.xlsx]
2024-08-12 Update wire connection.
2024-08-17 Modify the power indication.
2024-08-17 Power +- problem.
2024-08-20 Modify hardware bom.
    [BOM_PCB_Controller.csv, BOM_PCB_Encoder.csv, BOM_PCB_IMU.csv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]
2024-08-21 Add PCB cover stl part.
    [PCBCover(optional).stl]
